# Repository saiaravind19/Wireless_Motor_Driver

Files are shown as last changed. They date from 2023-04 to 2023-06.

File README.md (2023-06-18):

## Wireless Motor Driver ##

Motor Drivers are popular among Robotics/ Hardware Enthusiasts to build various cool projects. One of the most popular among them is the L298N motor driver. Conventionally, we use the motor driver, a bunch of wires and connect it to our microcontroller to control different actuators. But in our version of the Motor Driver, we have  made it into a one stop solution by removing the excess of wires and connecing the Wemos DI mini microcontroller, all in one single PCB!

Wemos D1 mini was chosen for it WiFi functionality. We have our own GUI through which the motor driver can be controlled. One of the main objective of making this Motor Driver was to reduce the time to prototype projects and also to make your bots completely wireless. You can simply connect the motors and control it via your mobile through WiFi. That's how simple it is!

<p float="left">
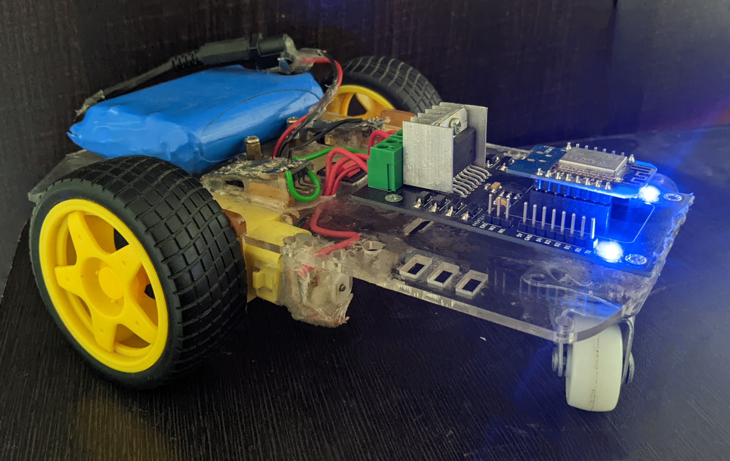
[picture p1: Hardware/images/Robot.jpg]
 
     
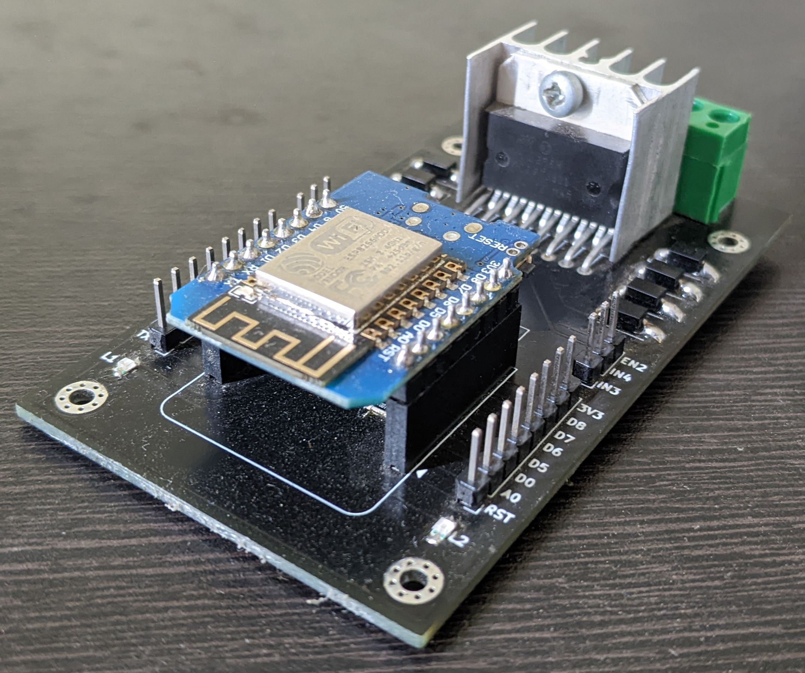
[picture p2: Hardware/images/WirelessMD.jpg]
Wireless Motor Driver
 
</p>

## Specifications
- Supply Voltage: 6 - 12V
- Output Current: 1.2A (max)
- 500mA Fuse Protection for Wemos D1 mini
- Can be used separately as a conventional L298N Motor Driver as well

## Prerequisites 
- Make sure you install one of the [supported version](https://www.arduino.cc/en/software/OldSoftwareReleases) of Arduino IDE and have ESP8266 core installed.
     - Package is tested with Arduino IDE v 1.8.5  <-> plugin v 0.5.0 so it is recommended to use the same.
- To install [Spiffs files uploader](https://github.com/me-no-dev/arduino-esp32fs-plugin) please follow installation tutorials provided in the tutorial.
- Once the plugging and Arduino IDE are installed successfully move on to next step of  installation of stack to controller.

## Installation
- Clone the repo to the system  and open the project in Arduino IDE.
  -  _**Note:Make sure data folder is present in current working directory.**_
- Use spiffs files uploader to flash the HTML UI to ESP. To upload navigate to Tools>ESP8266 Sketch Data Upload.
- Wait for the files to upload once the files are uploaded, compile and upload the program.
     - _**Note:Once the files are uploaded no need to reupload file each time a new code is flashed.**_ 

## Pinout Connections

| Controller Gpio  | MotorDriver pin|
| --- | --- |
| D1 | EN1 |
| D5 | IN1 |
| D6 | IN2 |
| D2 | EN2 |
| D7 | IN3 |
| D8 | IN4 |
| D3 | L1-led |
| D0 | L2-led |

## Accessing UI
- In case using ESP as Access point(AP mode) connect to the network SSID mentioned in the file **data>wifi>ap.txt** present in the working directory.
- Open your favourite web browser and type **wirelessmd.local** and the UI pops up in the browser and you are ready to control the motors wirelessely.

## Hardare
  All of the schematic and board layout files are present in this folder. The PCB was designed using KiCAD 6.0 version.
The board is based upon the popular Dual Full Bridge Motor Driver L298N and the miniature wireless microntroller development board Wemos D1 mini. The PCB can output nearly 1.2A per channel. Since it has the Wemos D1 mini on board, it gives the user the capability to control the motors wwirelessly using our unique GUI.

- WirelessMD/Hardware/KiCAD Project - Contains the KiCAD Project File 
- WirelessMD/Hardware/WirelessMD_sch.pdf - Schematic of Wireless Motor Driver PCB

## Demo Video

https://github.com/saiaravind19/WirelessMD/assets/73806646/1ec77462-335a-4383-b794-b8709d903f12

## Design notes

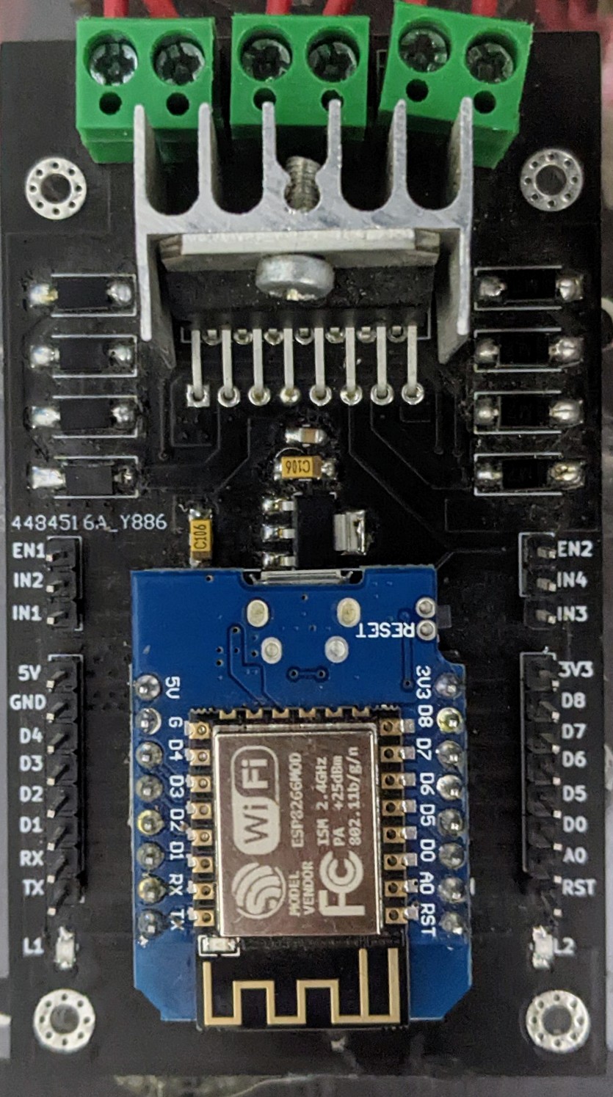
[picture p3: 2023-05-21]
Hardware/images/TopView.jpg

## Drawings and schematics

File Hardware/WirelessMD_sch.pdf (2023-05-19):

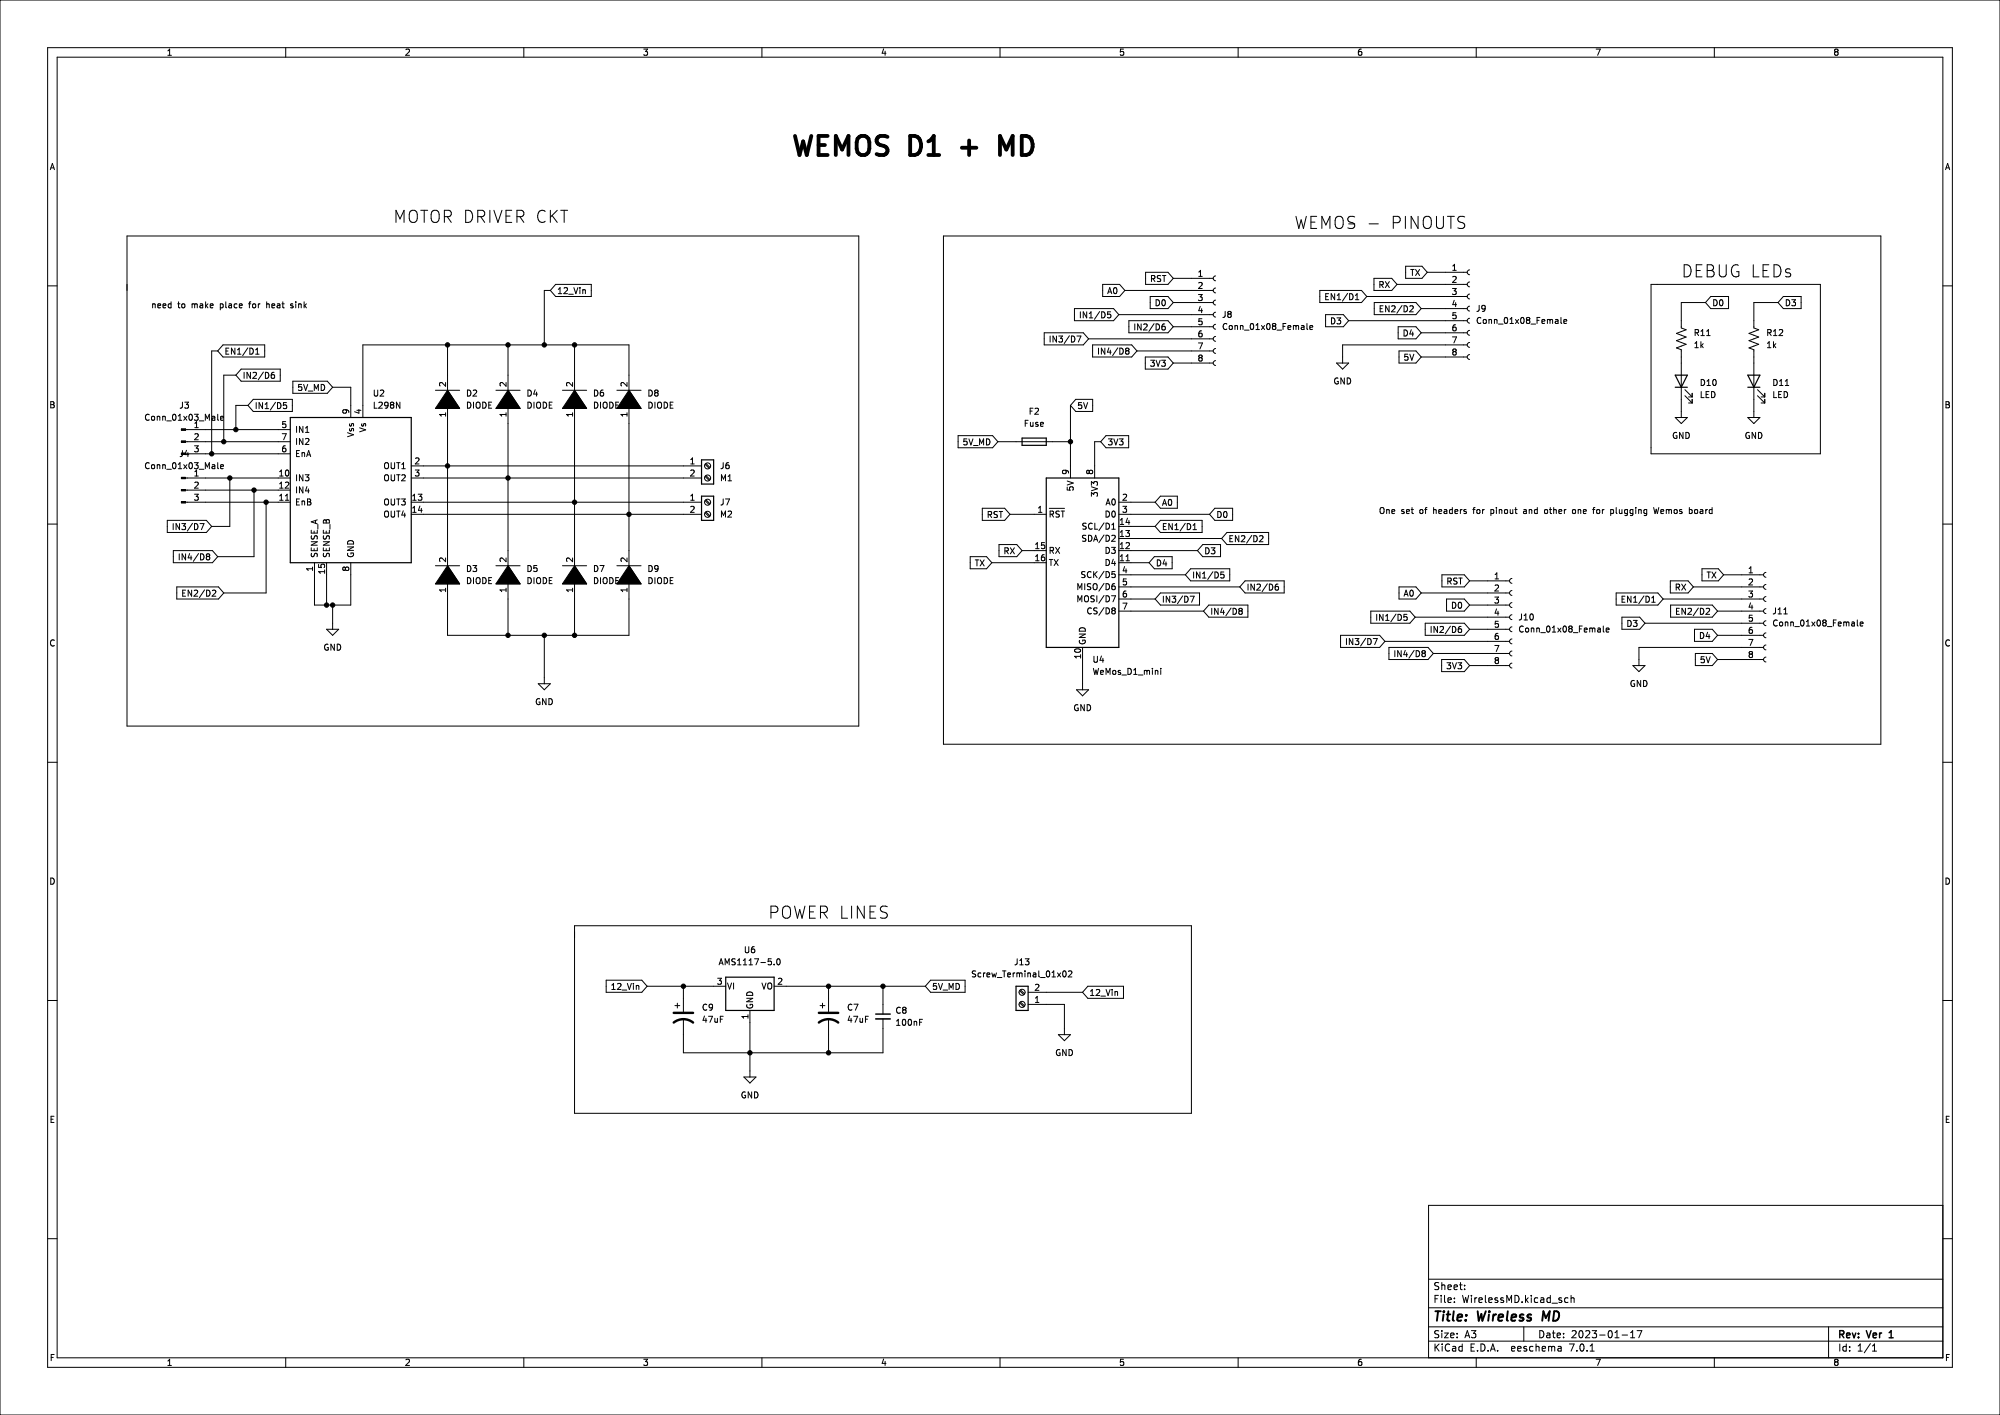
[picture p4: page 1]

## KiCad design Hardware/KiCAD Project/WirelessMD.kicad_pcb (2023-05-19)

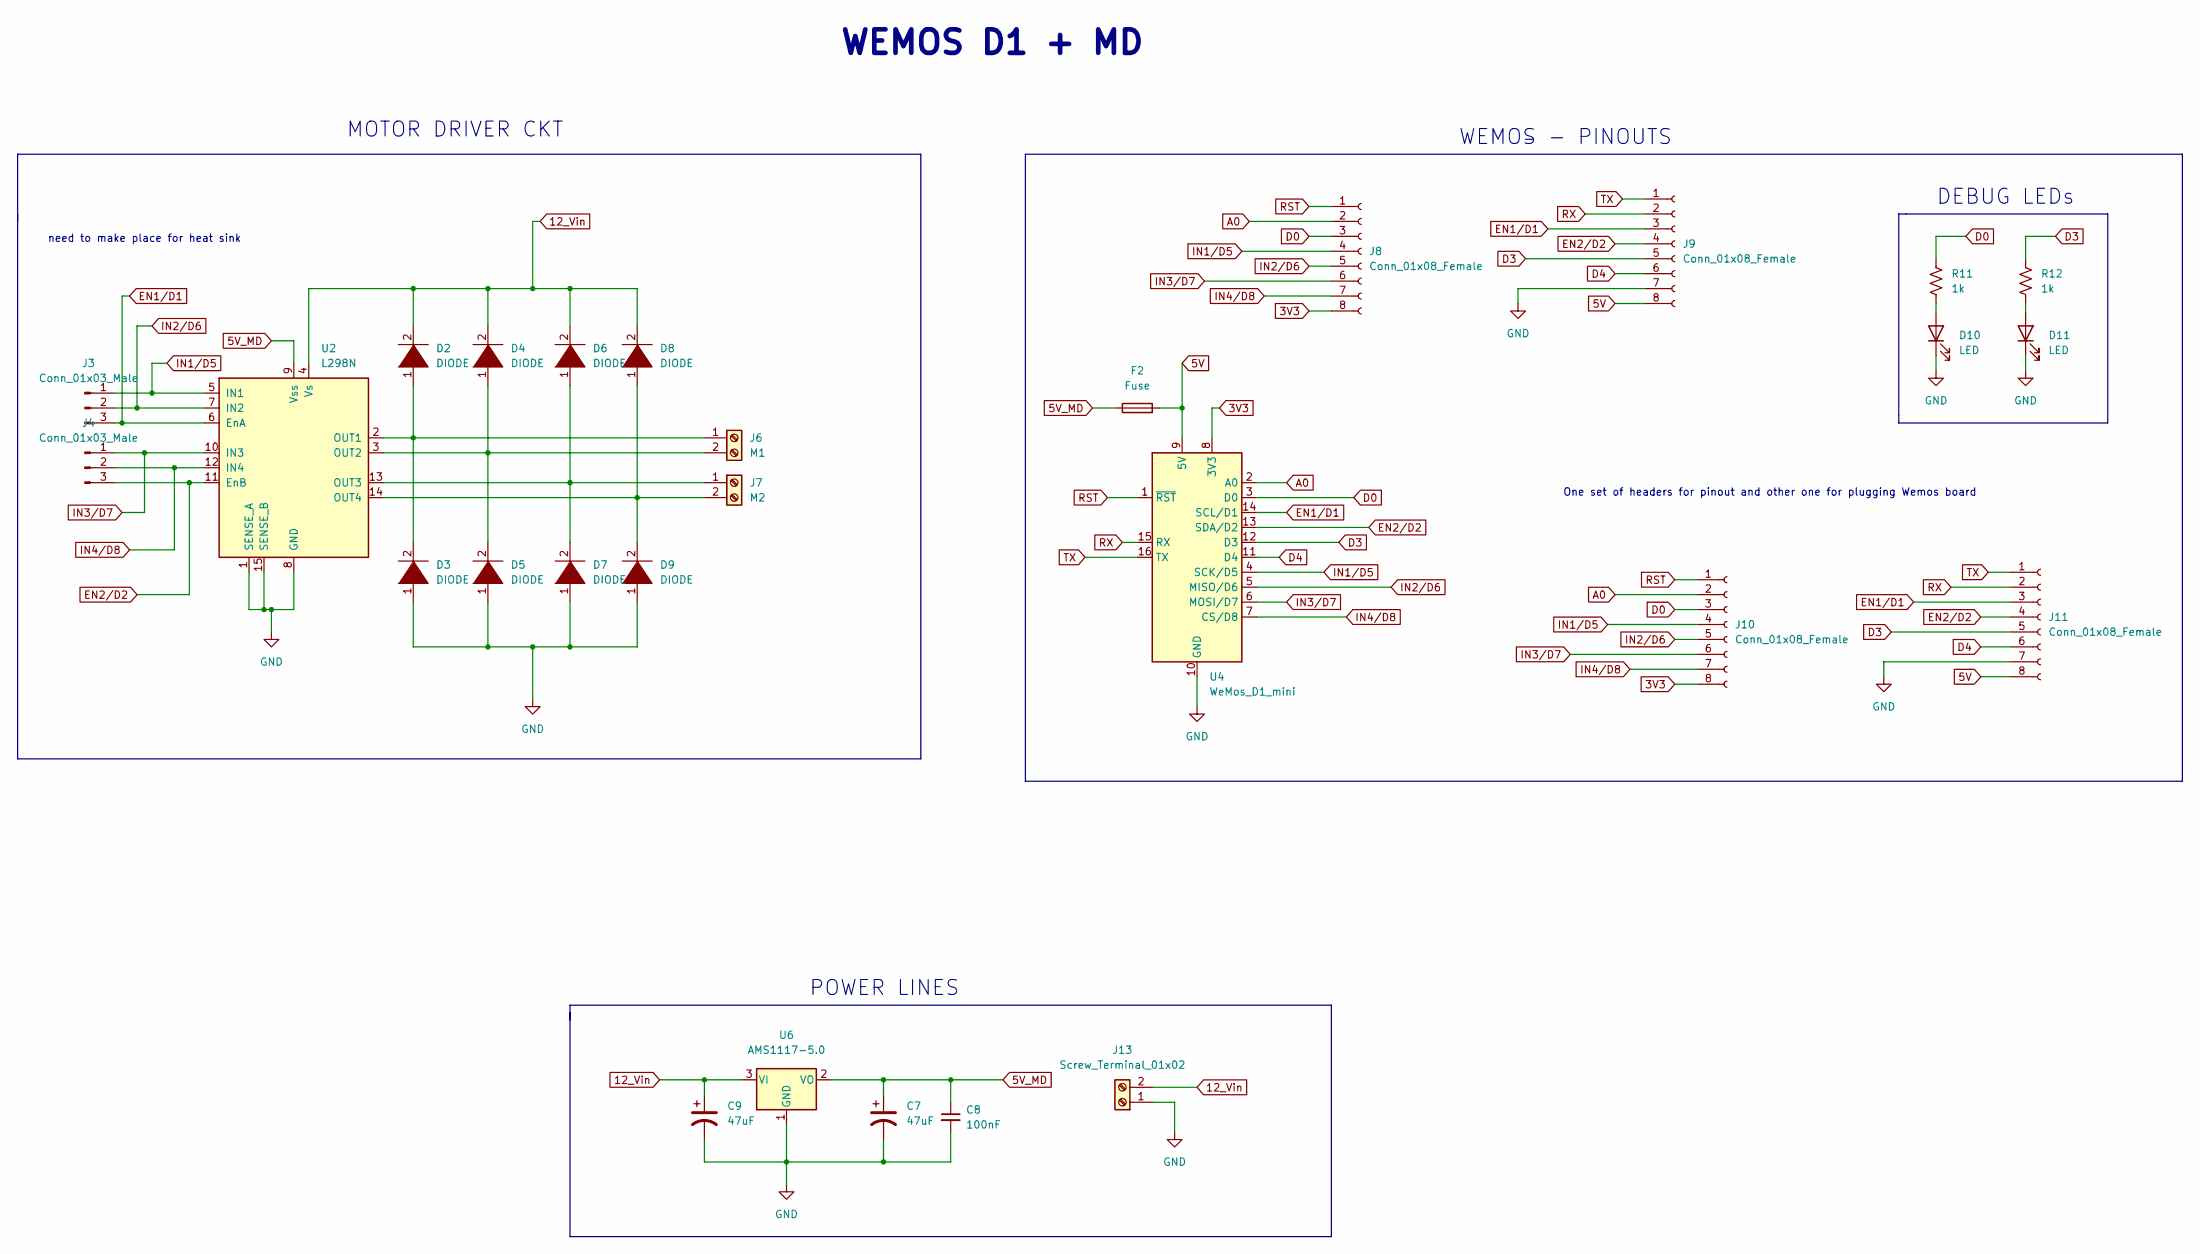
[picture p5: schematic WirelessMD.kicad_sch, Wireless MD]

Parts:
C7, C9: 47uF; 1206
C8: 100nF; 0805
D2, D3, D4, D5, D6, D7, D8, D9: DIODE; D_SMA_Handsoldering
D10, D11: LED; 0805
F2: Fuse; 1206
J3, J4: Conn_01x03_Male; PinHeader_1x03_P2.54mm_Vertical
J6: M1; TerminalBlock_bornier-2_P5.08mm
J7: M2; TerminalBlock_bornier-2_P5.08mm
J8, J9, J10, J11: Conn_01x08_Female; PinHeader_1x08_P2.54mm_Vertical
J13: Screw_Terminal_01x02; TerminalBlock_bornier-2_P5.08mm
R11, R12: 1k; 0805
U2: L298N; TO-220-15_P2.54x2.54mm_StaggerOdd_Lead4.58mm_Vertical
U4: WeMos_D1_mini; WEMOS_D1_mini_light
U6: AMS1117-5.0; SOT-223

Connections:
3V3: J8.8, J10.8, U4.8 (3V3)
5V: F2.2, J9.8, J11.8, U4.9 (5V)
5V_MD: C7.1, C8.1, F2.1, U2.9 (Vss), U6.2 (VO)
12_Vin: C9.1, D2.2 (A), D4.2 (A), D6.2 (A), D8.2 (A), J13.2, U2.4 (Vs), U6.3 (VI)
A0: J8.2, J10.2, U4.2 (A0)
D0: J8.3, J10.3, R11.2, U4.3 (D0)
D3: J9.5, J11.5, R12.2, U4.12 (D3)
D4: J9.6, J11.6, U4.11 (D4)
EN1/D1: J3.3, J9.3, J11.3, U2.6 (EnA), U4.14 (SCL/D1)
EN2/D2: J4.3, J9.4, J11.4, U2.11 (EnB), U4.13 (SDA/D2)
GND: C7.2, C8.2, C9.2, D3.1 (K), D5.1 (K), D7.1 (K), D9.1 (K), D10.1 (K), D11.1 (K), J9.7, J11.7, J13.1, U2.1 (SENSE_A), U2.8 (GND), U2.15 (SENSE_B), U4.10 (GND), U6.1 (GND)
IN1/D5: J3.1, J8.4, J10.4, U2.5 (IN1), U4.4 (SCK/D5)
IN2/D6: J3.2, J8.5, J10.5, U2.7 (IN2), U4.5 (MISO/D6)
IN3/D7: J4.1, J8.6, J10.6, U2.10 (IN3), U4.6 (MOSI/D7)
IN4/D8: J4.2, J8.7, J10.7, U2.12 (IN4), U4.7 (CS/D8)
unnamed: D2.1 (K), D3.2 (A), J6.1, U2.2 (OUT1)
unnamed: D4.1 (K), D5.2 (A), J6.2, U2.3 (OUT2)
unnamed: D6.1 (K), D7.2 (A), J7.1, U2.13 (OUT3)
unnamed: D8.1 (K), D9.2 (A), J7.2, U2.14 (OUT4)
unnamed: D10.2 (A), R11.1
unnamed: D11.2 (A), R12.1
RST: J8.1, J10.1, U4.1 (~RST)
RX: J9.2, J11.2, U4.15 (RX)
TX: J9.1, J11.1, U4.16 (TX)

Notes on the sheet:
POWER LINES
DEBUG LEDs
WEMOS - PINOUTS
need to make place for heat sink
MOTOR DRIVER CKT
WEMOS D1 + MD
One set of headers for pinout and other one for plugging Wemos board

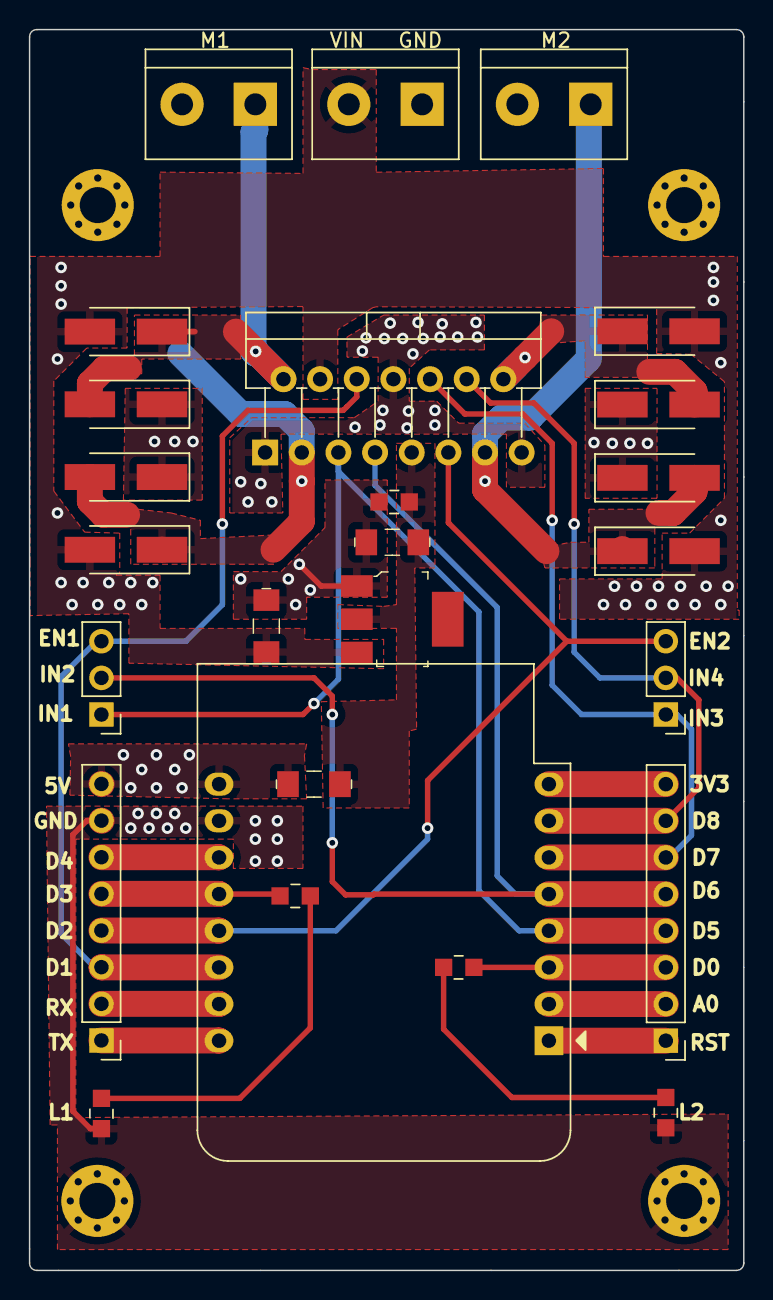
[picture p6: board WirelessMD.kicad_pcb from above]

Board: 2 copper layers, 49.5 x 86.0 mm, 26 parts (0 on the bottom side), 24 nets.

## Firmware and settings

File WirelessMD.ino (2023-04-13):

#include <ESP8266WebServer.h>
#include <FS.h>
#include <ESP8266WiFi.h>

#include <ESP8266mDNS.h>
#include "config.h"


IPAddress local_IP(192, 168, 4, 22);
IPAddress gateway(192, 168, 4, 9);
IPAddress subnet(255, 255, 255, 0);



ESP8266WebServer server (80);

struct wifiConfig {
  String ssid;
  String password;
};


//This function takes the parameters passed in the URL(the x and y coordinates of the joystick)
//and sets the motor speed based on those parameters.
void handleJSData()
{
  boolean yDir;
  int x = server.arg(0).toInt() * 10;
  int y = server.arg(1).toInt() * 10;
  int aSpeed = abs(y);
  int bSpeed = abs(y);
  //set the direction based on y being negative or positive
  if ( y < 0 ) {
    yDir = 0;
  }
  else {
    yDir = 1;
  }
  //adjust to speed of each each motor depending on the x-axis
  //it slows down one motor and speeds up the other proportionately
  //based on the amount of turning
  aSpeed = constrain(aSpeed + x / 2, 0, 1023);
  bSpeed = constrain(bSpeed - x / 2, 0, 1023);

  //use the speed and direction values to turn the motors
  //if either motor is going in reverse from what is expected,
  //just change the 2 digitalWrite lines for both motors:
  //!ydir would become ydir, and ydir would become !ydir

  Serial.print("x=");
  Serial.print(aSpeed);
  Serial.print("y=");
  Serial.println(bSpeed);


  //MotorA
  digitalWrite(AIN1, !yDir);
  digitalWrite(AIN2, yDir);
  analogWrite(PWMA, aSpeed);

  //MotorB
  digitalWrite(BIN1, !yDir);
  digitalWrite(BIN2, yDir);
  analogWrite(PWMB, bSpeed);

  //return an HTTP 200
  server.send(200, "text/plain", "");
}


void stopDriver(){
  analogWrite(PWMA, 0);
  analogWrite(PWMB, 0);  
}


struct wifiConfig get_id_pass(String filepath)
{
  wifiConfig ap;
  //Serial.println(filepath);
  File file = SPIFFS.open(filepath, "r");
  ap.ssid = file.readStringUntil('\n');
  ap.password = file.readStringUntil('\n');
  file.close();
  return ap;
}

void reset_controller()
{
  Serial.println("Reset pressed");
  server.send(200, "text/plain", "");
  ESP.restart();

}

void initGpio()
{

  pinMode(PWMA, OUTPUT);
  pinMode(AIN1, OUTPUT);
  pinMode(AIN2, OUTPUT);

  pinMode(PWMB, OUTPUT);
  pinMode(BIN1, OUTPUT);
  pinMode(BIN2, OUTPUT);
}

void writeToFile(String id, String pass)
{ String t_location = "/wifi/temp.txt";
  File temp = SPIFFS.open(SAPfile, "w");
  Serial.print("id length:");
  Serial.println(id.length());


  Serial.print("password length:");
  Serial.println(pass.length());

  if (!temp) {
    Serial.println("Error opening file for writing");
    return;
  }
  else
  {
    temp.println(id);
    //temp.print(',');
    temp.println(pass);
    temp.close();
  }
  SPIFFS.gc();

}

void getSapdata()
{
  Serial.println(server.args());

  String ssid = server.arg("ssid");
  String password = server.arg("password");
  Serial.println(ssid);
  Serial.println(password);
  server.send(200, "text/plain", "");
  writeToFile(ssid, password);

}

void apconnect()
{
  if (WiFi.getMode() != WIFI_AP)
  {
    server.stop();
    set_apmode();
    beginWebserver(1);
  }
}

void staconnect()
{

  if (WiFi.getMode() != WIFI_STA) {
    server.stop();
    set_stamode();
    beginWebserver(1);
  }

}

void beginWebserver(bool mode_flag)
{

  set_dns();
  initGpio();

  server.serveStatic("/", SPIFFS, "/home.html");

  //call handleJSData function when this URL is accessed by the js in the html file
  server.on("/home.html", reset_controller);

  server.serveStatic("/mode/", SPIFFS, "/mode.html");

  server.serveStatic("/ap_home/", SPIFFS, "/ap_home.html");


  server.serveStatic("/ap_home/view/", SPIFFS, "/displayap.html");
  server.serveStatic("/sap_home/view/", SPIFFS, "/displaysap.html");


  server.serveStatic("/sap_home/", SPIFFS, "/sap_home.html");
  server.serveStatic("/sap_home/form/", SPIFFS, "/form.html");


  server.on("/ap_home/ap_home.html", apconnect);
  server.on("/sap_home/form/form.html", getSapdata);
  server.on("/sap_home/sap_home.html", staconnect);


  server.serveStatic("/control/", SPIFFS, "/joystick.html");

  server.serveStatic("/control/virtualjoystick.js", SPIFFS, "/virtualjoystick.js");
  //call handleJSData function when this URL is accessed by the js in the html file
  server.on("/control/jsData.html", handleJSData);
  server.begin();
}

bool filecheck(String filepath) {
  return SPIFFS.exists(filepath);
}

void AP_mode(struct wifiConfig apSettings)
{

  WiFi.mode(WIFI_OFF);

  Serial.print("SSID:");
  Serial.println(apSettings.ssid);
  Serial.print("PASSWORD:");
  Serial.println(apSettings.password);

  WiFi.mode(WIFI_AP);
  Serial.println(WiFi.softAPConfig(local_IP, gateway, subnet) ? "Ready" : "Failed!");

  WiFi.setAutoConnect(false);
  WiFi.setAutoReconnect(false); // if wifi attempts to (re)connect to a previous router it kills the access point


  WiFi.softAP(apSettings.ssid, apSettings.password, 10, false, 1);
  Serial.print("Setting AP ... ");
  Serial.print("AP IP address = ");
  Serial.println(WiFi.softAPIP());
}

void wait_for_dns() {
  while (1) {
    delay(1000);
    Serial.println("[ERROR] MDNS responder did not setup for ap mode ");
  }

}

void set_dns()
{

  if (WiFi.getMode() == WIFI_AP) {
    if (!MDNS.begin("wirelessmd", WiFi.softAPIP())) {
      Serial.println("[ERROR] MDNS responder did not setup for ap mode ");
      wait_for_dns();
    }
    else Serial.println("DNS server successfully created for AP mode");
    
    MDNS.addService("http", "tcp", 80);
  }
  else {
    if (!MDNS.begin("wirelessmd")) {
      Serial.println("[ERROR] MDNS responder did not setup STA mode");
      wait_for_dns();
    }
    else  Serial.println("DNS server successfully created for STA mode");
  }
}


void set_apmode()
{
  struct wifiConfig apSettings;

  if (!filecheck(APfile) )
  {

    Serial.println("failed to open AP and SAP settings defaulting ssid and password");
    apSettings.ssid = "ESP8266";
    apSettings.password = "Helloworld";
    AP_mode(apSettings);
  }
  else
  {
    apSettings = get_id_pass(APfile);
    AP_mode(apSettings);
  }

}


bool set_stamode()
{
  struct wifiConfig apSettings;
  bool mode_flag = 0;
  int retries = 30;

  Serial.println("running ESP in SoftAP mode");
  apSettings = get_id_pass(SAPfile);
  Serial.print("connecting ESP to:");
  Serial.print(apSettings.ssid);
  Serial.print("PASSWORD:");
  Serial.print(apSettings.password);

  delay(2000);

  WiFi.mode(WIFI_STA);

  WiFi.setAutoConnect(true);
  WiFi.setAutoReconnect(true); // if wifi attempts to (re)connect to a previous router it kills the access point


  //WiFi.begin(id,pass);     //Connect to your WiFi router
  WiFi.begin(apSettings.ssid.c_str(), apSettings.password.c_str());    //Connect to your WiFi router
  while (WiFi.status() != WL_CONNECTED && retries > 0) {
    delay(1000);
    Serial.print(".");
    retries -= 1;
  }
  Serial.println();
  if (retries == 0) {
    Serial.println("failed to connect to network in SoftAp mode chnaging to ap mode");
  }
  else {
    mode_flag = 1;
    Serial.println("WiFi connected");
    Serial.println("IP address: ");
    Serial.println(WiFi.localIP());
  }
  //set ap mode if sta mode is failed
  if (WiFi.status() !=  WL_CONNECTED) {
    set_apmode();
  }

  return mode_flag;
}


void setup()
{
  bool mode_flag = 0;
  WiFi.mode(WIFI_OFF);
  Serial.begin(115200);
  delay(2000);

  if (!SPIFFS.begin())
  {
    Serial.println("SPIFFS Mount failed");
    ESP.restart();
  }
  else
  {
    Serial.println("SPIFFS Mount succesfull");
  }

  if (!filecheck(SAPfile)) {
    Serial.println("failed to open SoftAP changing mode to AP");
  }
  else {

    mode_flag = set_stamode();
  }


  beginWebserver(mode_flag);
}

void loop()
{
  MDNS.update();
  server.handleClient();

}

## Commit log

2023-02-05 implemented start button in the hoem page
2023-02-08 fix for wifi module reset on AP mode
    [WirelessMD.ino]
2023-02-13 Fix for sap mode
    [WirelessMD.ino]
2023-02-18 added home button to joystick page
2023-02-26 added home button in mode page
2023-04-13 Update README.md
    added arduino older version link
2023-05-21 added motor driver picture
2023-05-21 Update README.md
    added motor driver image
